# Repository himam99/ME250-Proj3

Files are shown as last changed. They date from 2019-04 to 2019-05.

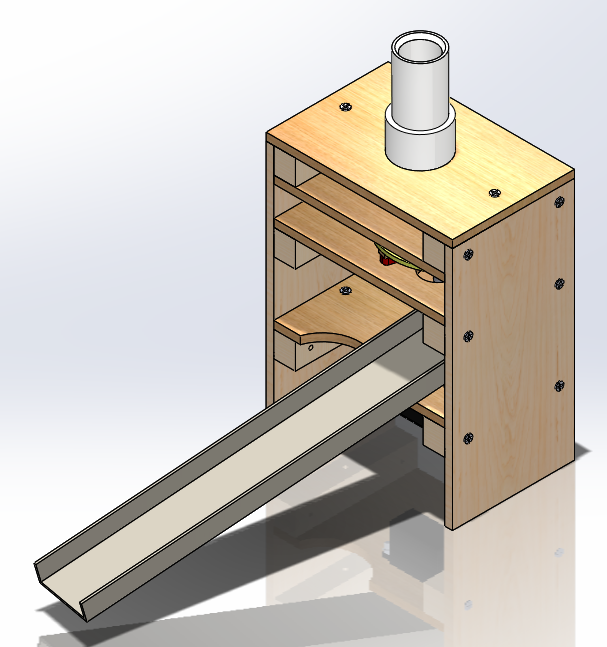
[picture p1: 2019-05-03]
LaTeX/Images/assembly_AB.png

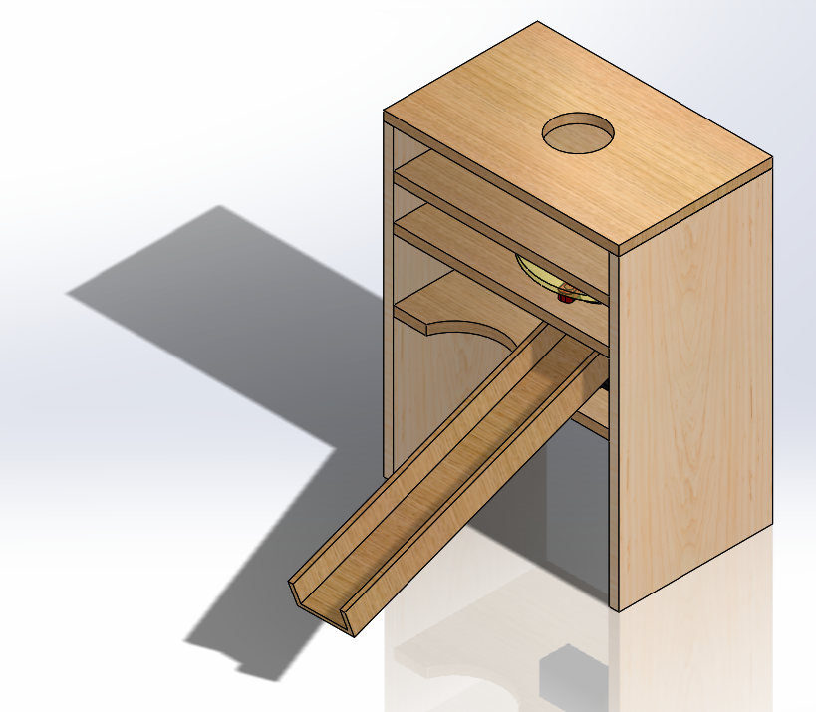
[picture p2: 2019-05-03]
LaTeX/Images/assembly_IP.png

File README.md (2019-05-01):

# ME250 S19 Project 3: Color Sorter

**Project 3: Color Sorter** for ME 250 at the University of Illinois at Chicago for the Spring 2019 semester.

This repository contains:
  - all Arduino (.ino) files used, either for testing or for the final product,
  - all CAD models (misc SolidWorks extensions), with different stages of development grouped seperately, and
  - all LaTeX files (.tex, .png for inset images, .pdf for output) used to generate the final report.
  
This project was made using Arduino, SolidWorks, Notepad++, and Overleaf.

Although this repository was created by me, some of its contents were made by other members of Group 17, and many other parts of the project could not have been done without their help.

Hammad Imam // himam4@uic.edu    
Group 17     
Undergraduate, Mechanical Engineering    
May 3rd, 2019

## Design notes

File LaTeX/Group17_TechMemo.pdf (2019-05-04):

# Project 3 Tech Memo: Color Sensor

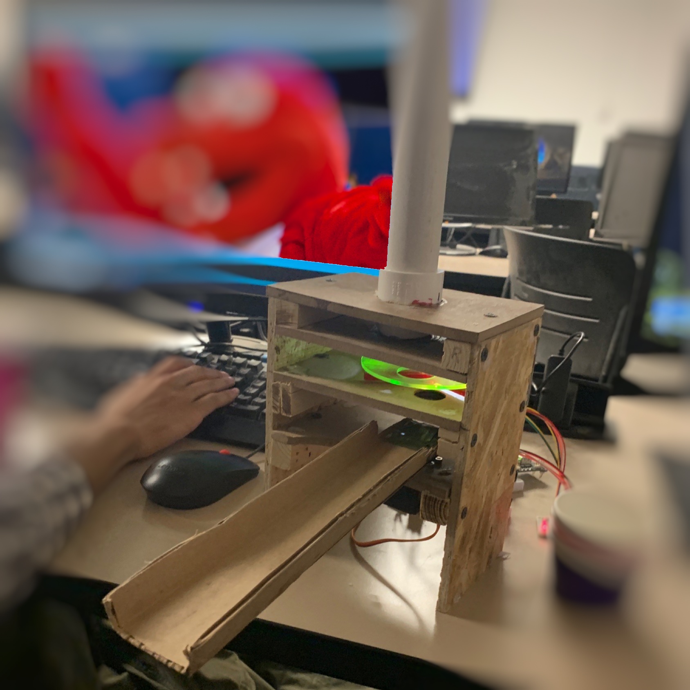
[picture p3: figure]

May 3rd, 2019.

# Team #17 The Three-Droppers Jos´e Luis G´omez Hammad Imam Thihan Moe Kyaw Daniel Spathies

# ME 250 Section #2 Professor Szwalek

## Executive Summary

The overall purpose of this project was to create a device that would sort balls by their color. This project is part of the curriculum for ME 250: Intro to Engineering Design and Graphics during the Spring 2019 semester at the University of Illinois at Chicago.

This report begins with an introduction on the background of the project. Next is the problem definition section, which details how the group identified constraints and objectives, and what metrics were used to define them. An objectives tree is given to detail how the group identified different objectives used in the development of the project. The problem definition section is followed by the functional analysis, which includes definitions of functions as well as a functions-means tree for the functions and means that the group brainstormed. Then, the report highlights how concepts were generated and narrowed down into the final design. The final design section is broken into mechanical, electrical, and cost subsections. The mechanical design subsection details how the physical aspects of the device were designed, from the initial sketch to a detailed CAD assembly. Dimensioned CAD drawings are provided to show more detail on the final product. The electrical design subsection describes how the components were wired and configured, and provides a wiring diagram so it can be seen how the wiring was done. It also contains a section on code which describes the main functions and algorithms used in the device. The final subsection of the final design is the cost, which provides both the dollar value of the constructed materials, and the environmental impact of the creation of the device. After the device design has been thoroughly explained, the changes and improvements made while testing are given so the stages of the design process can become clear to the reader. The report summarizes with a conclusion of the work done in the project and the lessons the group learned from working on it.

From the report, we can gather how a device like this might be created, going from how it was determined what it should do to how it was initially created to how it was modified to improve its performance. The major conclusions that can be drawn are that a project like this is very time consuming and requires good foresight so that nothing is unplanned for. Projects like this also require proper time management so that any issues that arise can be discovered and dealt with and still be completed in a timely manner. The major lessons learned from this project are both technical skills, as this project required coding, building, and testing knowledge that not all group members previously had; and time management skills, as many aspects of this projects went over the time constraints we had initially planned for. In the future, the group members will use these skills to improve their performance in engineering projects, both those related to academia and in industry.

Overall this project was a good learning opportunity for the team and a lot was accomplished. The device unfortunately did not have all aspects properly functional by the end of the project, but the group learned a lot through the design process and noticing what went wrong. This report aims to detail how the group went through the design process, what was changed during the design phase, and the lessons that were learned throughout the project.

## Contents

1 Introduction | 4
2 Problem Definition | 5
3 Functional Analysis | 7
4 Concept Generation | 9
5 Final Design | 17
6 Device Testing | 28
7 Conclusions | 29
A References | 30
B Code | 30
C CAD | 33

## 1 Introduction

This tech memo is on the creation of a color sorting device that should be able to sort rubber balls by their color. This project was assigned to the team through a mechanical engineering course, the limitations in concepts, materials, and functions of the device are created by the course project guideline. Material limitations are limited to what has been listed as acceptable in one of the handouts given by the course managers and instructors. The time for the brainstorming and development of the device was also limited as it was limited to when we were told about the nature of the project. This project is the summation and an application of much of the knowledge and skills that were taught in the course. There were two projects that involved writing a technical memo on a reversed engineered device and on an experiment. They served as practice for learning how to write a technical memo. The course had CAD Solidworks, Arduino UNO, and workshop lessons which would all be applied in this project. The manufacturing of the components of the device was limited to 3D printing, the courses’ workshop materials and tools, and laser cutting.

The main objective of this report is to give an extensive and comprehensive explanation of the process that was taken to create the final device given the limitations and primary objective. The sub-objectives of this report, which function to accomplish the main objective, can be divided based on each section of the report. The first following section is Problem Definition, the purpose of this section is to define what the problem is in a better sense by explicitly stating the limitations of the project, creating objectives of multiple levels, and metricizing those objectives to quantify the satisfaction of those objectives. The primary culmination of this section is the objectives tree which shows all of the objectives in their order of relation and importance. The following section is Functional Analysis which is where the team begins to define what the device will perform and the possible means by which the device can perform those functions, this culminates in a Functions-means tree which gives you a layout of how the functions and means are interconnected. The next section is Concept Generation and Selection, this section is where the expansion and then contraction of ideas is done to find the best possible design concept. The expansion is done by creating a morphological chart that lists all the possible means for each of functions of the device. The morph chart is then reduced by accounting for illogical and unreliable means combinations. From the remaining possibilities a list is created of the top twenty, then one of the top five with designs images for each of them. Finally, a comparison chart of the top five concepts is created to find the top device concept. The following section is Final Design. In this section the physical design process of the top concept is explained through CAD models and explanation on modifications. The software and hardware configurations are explained in detail and finally a Bill of Materials table is created which has physical, economical, and environmental properties of each of the parts of the device, excluding hardware and software. The next section is Device Testing, this section is where the findings of trials and the decisions of modifications to the device in light of these findings are documented. The section that follows is the Conclusion of the report which should review the findings of the report, state any of the limitations of this project and suggest any improvements that could be done to this project. Finally, the report ends with References and an Appendix containing detailed information on the software used.

## 2 Problem Definition

### 2.1 Introduction

This section of the report is meant to define and clarify the main problem of the designing of the device. The objectives, metrics, and constraints of the designing project are stated here as they give the main context needed to define the problem. The objective tree shows all the objectives of the device in hierarchical order and grouped according to their sub-sectionality of each other. All the ideas that have been generated by the designing team have been added to the objectives tree as the purpose of the objective tree is to give a graph of all the possible objective paths that can be taken to fulfill the primary objective.1 Affinity mapping was the method used to create the objective tree. This process begins by having the objectives generated through brainstorming possible objectives and writing each one down on a sticky note. These objectives are then sorted into categories and placed according to priority.

The team was tasked with creating a device to autonomously sort bouncy balls by color into a predetermined number of cups. Certain considerations must be taken into account in designing such a device like using the most eco-friendly materials, manufacturing at the cheapest price and making a safe usable device that functions without input from team members.

### 2.2 Definitions

Metric: A standard of measurement; in the context of engineering design, a scale on which the achievement of a designer’s objectives can be measured and assessed.

Constraint: A limit or restriction on the design’s behaviors or attributes

Objective: A feature or behavior that the design should have or exhibit

### 2.3 Metrics

Metrics are the quantification of the stated objectives, this facilitates a comprehension of the level of success of the objectives.

- Cost efficiency: cost in dollars
- Time Efficiency: Time in seconds
- User Experience: On a scale from one to ten, ten being the greatest ease of use, reusability, and transportation of the device
- Functionality: Based on the percentage of balls that were successfully sorted to the amount of balls to be sorted, how accurate or effective is this device at achieving its function
- Designer experience: Scale from one to ten, ten being the best and easiest device to construct and build.

### 2.4 Constraints

The constraints are the limitations to the means by which the device will function.The constraints for the building of this device are:

- The device must be attached to the storage bin(hopper).
- The materials that can be used are limited to the ones found in a list.
- The quantity of each of the materials is limited to what is set on the aforementioned list.
- Energy used to power the device is limited to mechanical, electrical, and/or chemical energy.
- The device must be able to perform its primary objective autonomously

### 2.5 Objectives Tree

The following diagram is the visual description of the hierarchical order, based on contribution to solving the problem, and sub-sectionality relations of all objectives of primary, secondary, tertiary, etc., order. between all the objectives.

Table 4.3.1 - Morphological Chart

The primary objective of the device is on the top of the diagram. It is to make a machine that can sort by color. The lowered ordered objectives are objectives that can facilitate this primary objective and/or are objectives desired by the designers. These objectives have been limited to those which can be metricized for evaluation of the success of each objective for further development. The four main secondary objectives are efficiency, user experience, designer experience, and functionality. Under these objectives there are multiple objectives that are subsections of these four secondary objectives. It should be noticed that none of the objectives in the objectives tree are necessary elements of the device. This is due to the clear distinction between objectives and constraints, as they are defined above. There is only one primary objective which is the main answer to the problem statement.

### 2.6 Conclusion

To conclude this section, the metrics, constraints and objective tree are the parts of this section which give the context of the problem, something important for final analysis on determining how to go about solving the problem. The objective tree is important for understanding the hierarchical order and subsectional relationships of the objectives. The metrics and constraints sections of this section are also important as they help the designer understand what they are limited to and how it is that they can evaluate the success of their objectives.

## 3 Functional Analysis

### 3.1 Introduction

This section is on the functions and means of the device. The primary functions that the device is supposed to perform as well as the sub functions that the corresponding means will need are listed. The meaning of functions and means as they are used in this report refer specifically to engineering design and so are defined in this section for clarification. The functions and means are presented in a tree diagram which is meant to highlight the ranking of importance/order of the functions and link the means to their corresponding function.

### 3.2 Definitions

(Basic/Primary) Functions- what a device is supposed to do, should be described using verbs.

Means- The ways by which primary functions can be implemented, should be described usingnouns.

Secondary/sub functions- Functions that are governed by the means of the basic functions[2].

### 3.3 Function-Means Tree

The function-means tree is meant to give order to all the types of functions and their corresponding means. The order is based on the purpose of the function. Functions that serve the purpose of mitigating or completing other functions are secondary functions. All others are basic primary functions. Figure 3.3.1 is the functions mean tree for this projects device. The tree starts by giving primary functions in bolded text in rectangular boxes. More specific functions that explain the pieces of the primary functions are then given in underlined text in rectangular boxes. Means for each function are in plain text trapezoidal boxes below each function. Additional sub functions specific to each means are then given in plain text in rectangular boxes.

Tree outline

- Power Device
- Contain Structure

– Resist forces

– Join main structure

- Load balls in from hopper

– Couple from hopper
– Release balls from hopper
- Sort by color

– Determine color
– Release from color determiner
- Send ball to cup

– Determine where balls go
– Aim ball to cup

– Move ball to guide
– Guide ball to cup
– Resist forces while guiding ball

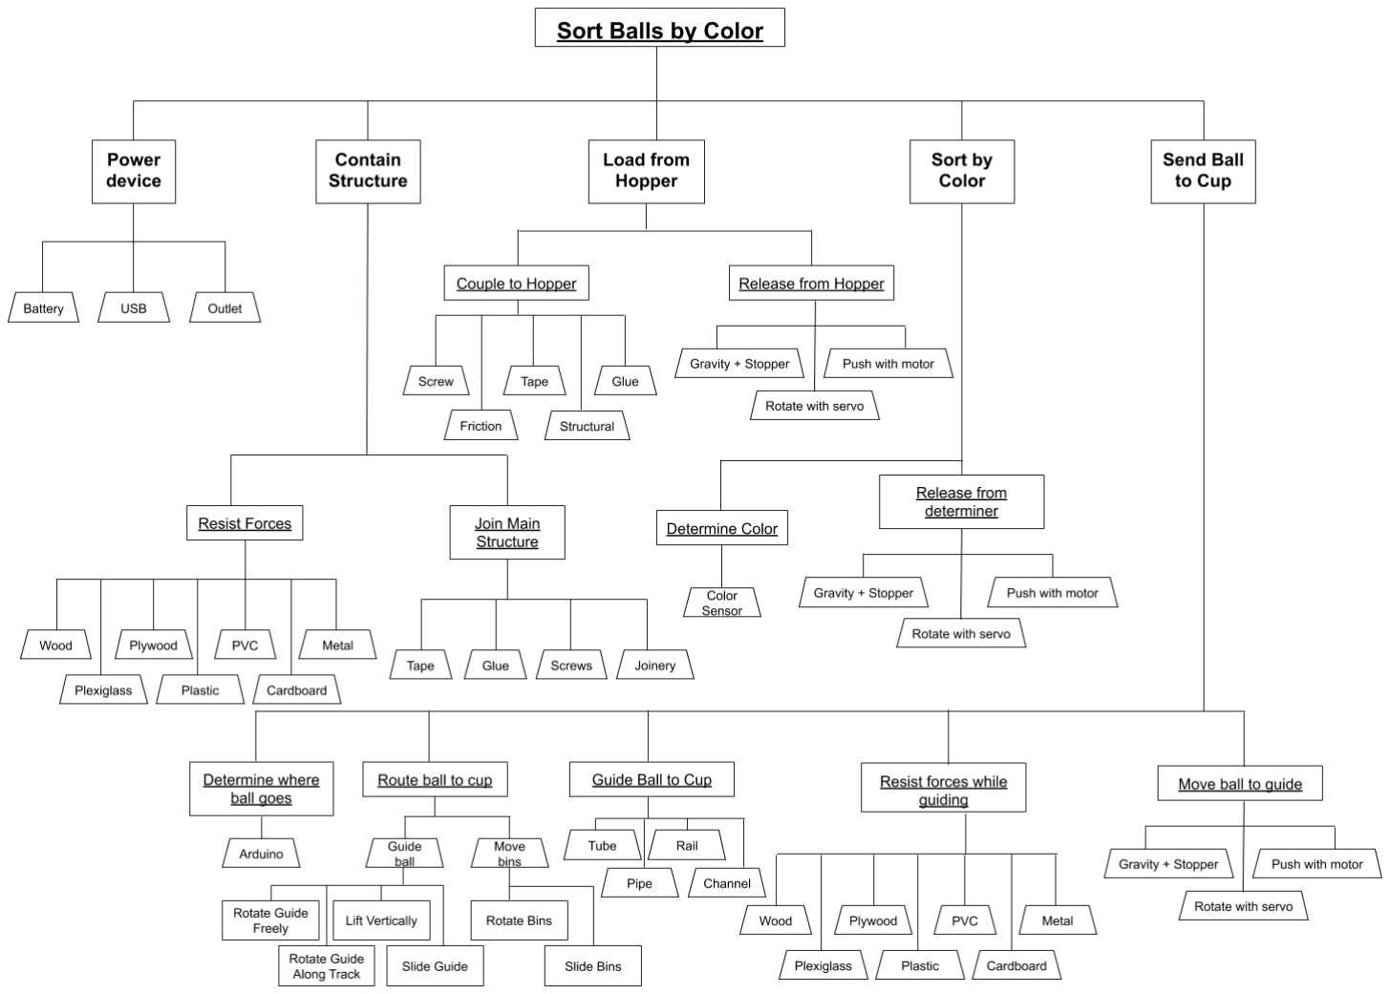
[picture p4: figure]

Figure 3.3.1 - Functions-Means Tree Full size available here. (https://raw.githubusercontent.com/himam99/ME250-Proj3/master/LaTeX/Images/functionmeans.png)

## 4 Concept Generation

### 4.1 Introduction

This section’s purpose is to present the procedure that was taken to select the concept design for the color sorting device. In this section, a morphological chart is used to generate all the possible design concepts by listing all the functions and their corresponding means. From this the top twenty or so concepts are chosen through an analysis on their practicality and ability to satisfy objectives. These concepts are listed in this section. From this a list of the top five concepts are chosen through more rigorous application of the same analysis as beforehand, these top five are also listed and justified. Finally, through the use of comparison charts the top concept is selected for manufacturing the device.

### 4.2 Definitions

Morphological chart: A matrix in which the leftmost column is a list of all of the principal functions that our design must perform and also some of the key features it must have.
Design space: An imaginary intellectual region of design alternatives that contains all of the possible solutions to the design problems[3].

### 4.3 Morphological Chart

The leftmost column of the chart shows the functions that should be included in the design. To the right of the functions are the all different types of means that were found which could perform the functions. The purpose of this chart, Figure 4.3.1 is to aid in expanding the design space.

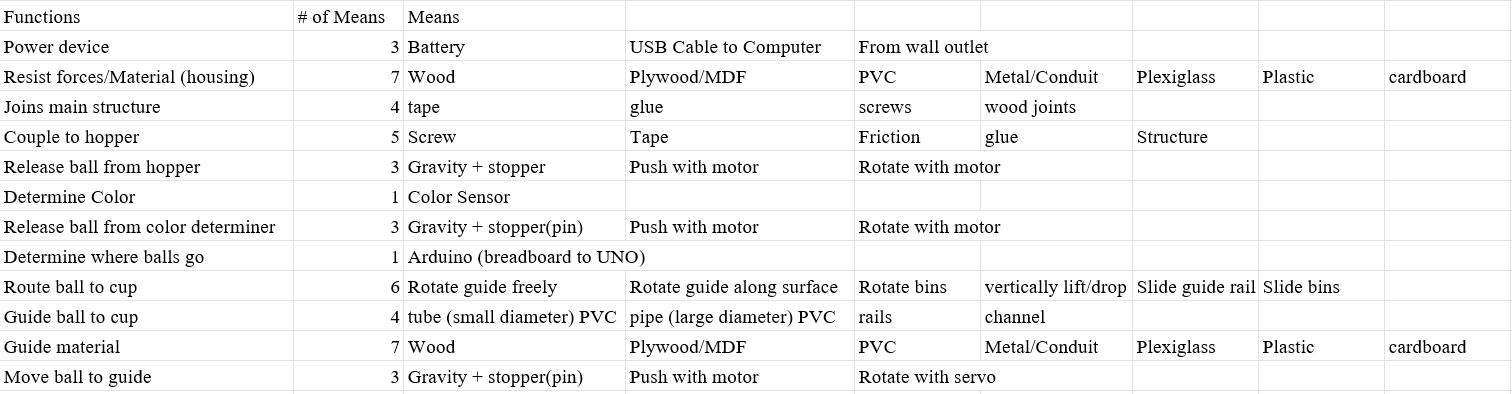
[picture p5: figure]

Table 4.3.1 - Morphological Chart

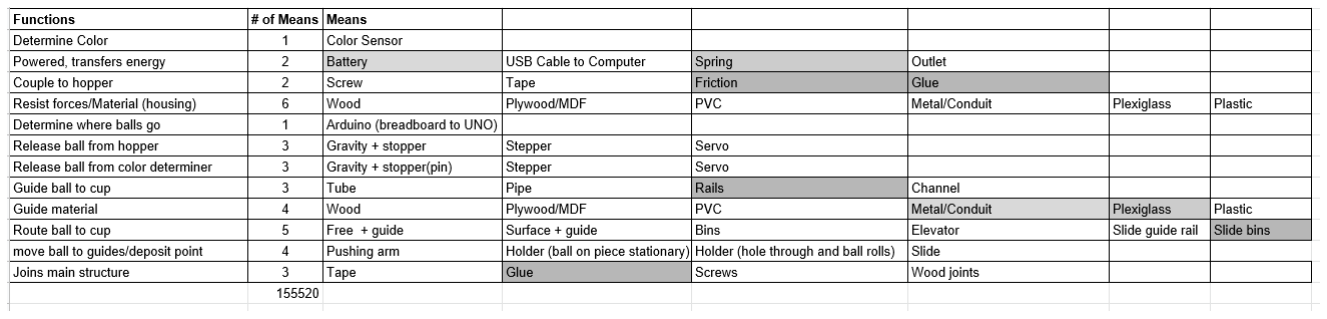
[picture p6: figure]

Table 4.3.2 - Reduced Morphological Chart

For Figure 4.3.2, the majority of the reductions in means are ones that are unreliable and impractical both relative to other means and somewhat objectively. For example, glue is not strong enough to withstand the forces on the main structure, so it was eliminated from the morph chart.

### 4.4 Concept List

- Wood housing using screws as main joiner, the color sorter is under the hopper, the ball then drops on an arm attached to a servo. The servo then rotates the calculated amount to one of the three fixed pvc pipes that lead to a cup.
- Cardboard housing using duct tape as main joiner, after color is sensed, a cardboard channel is moved by a servo to align with the proper cup and then the ball is released from the color determining area and then goes down the channel into the correct cup
- Wood housing with screws as main joiner, also there are fixed ramps made of cardboard, the ball moves from hopper to color sensor, then the ball gets released and gets deviated dependant on arduino code to go down a different ramp which will lead to a corresponding cup
- PVC housing with glue and tape as main joiners, this device acts as an elevator or dumbwaiter, after determining the color at the top of the shaft, this device drops the ball a determined height into the right cup, a servo with string can be used to lower or raise elevator shaft to desired position.
- Wooden housing with plastic, a spring and glue or tape as joiners, this device brings a ball from the hopper to the color sensor then drops it into a waiting catapult arm with a spring attached. The arm is pulled back at the precise distance to allow the ball to fly as a projectile and land in the correct cup, the arm is then winched back with a motor to an arduino determined distance and repeated.
- Wooden housing, a type of manufactured belt, metal to make conveyor and cardboard with various joiners being required. First, a single ball is deposited from the hopper and dropped onto a rotating conveyor belt that moves the ball to the right, the ball passes under the color sensor and the color is determined and then the arduino and code process the color and move a moveable ramp/platform at the end of the conveyor to bounce the ball into the correct cup.
- Wooden housing, a type of manufactured belt, metal to make conveyor and cardboard with various joiners being required. Similar to the other device using a conveyor, this device releases a ball onto the moving conveyor belt, scans the color and continues down the conveyor but next one of three motors is turned on and when it senses motion, extends to push to ball off the side of the conveyor into the correct cup.
- Wooden housing with screws or tape as main joiner, after scanning the color of the ball in the color scanning portion of the device, the ball is then dropped onto a ramp with a very small slope or angle and as the ball slowly travels down the ramp, the servo corresponding to the correct cup then moves and opens a hole for the ball to fall through into the cup below it
- Wooden housing with screws as main joiner, after ball’s color is sensed, the ball drops onto an arm attached to a servo, the arm rotates to be over the correct cup and then the servo on the arm activates, opening a hole in the arm, releasing the ball into the correct cup
- Cardboard housing with glue and tape and main joiners, the ball gets released from hopper, color gets sensed and then after being released from the color sensing station, the ball is redirected by a servo with an extended arm to push the ball down of of the three separate paths of the connected ramp into the desired cup

Top 5 Concepts

- Tri-Tube - Wood housing using screws as main joiner, the color sorter is under the hopper, the ball then drops on an arm attached to a servo. The servo then rotates the calculated amount to one of the three fixed pvc pipes that lead to a cup.
- Moving channel - Cardboard housing using duct tape as main joiner, after color is sensed, a cardboard channel is moved by a servo to align with the proper cup and then the ball is released from the color determining area and then goes down the channel into the correct cup

- Conveyor belt - Wooden housing, a type of manufactured belt, metal to make conveyor and cardboard with various joiners being required. First, a single ball is deposited from the hopper and dropped onto a rotating conveyor belt that moves the ball to the right, the ball passes under the color sensor and the color is determined and then the arduino and code process the color and one of three motors pushes the ball when motion is sensed into the correct cup
- Arm controller - Wooden housing with screws as main joiner, after ball’s color is sensed, the ball drops onto an arm attached to a servo, the arm rotates to be over the correct cup and then the servo on the arm activates, opening a hole in the arm, releasing the ball into the correct cup
- Tri-fold ramp- Cardboard housing with glue and tape and main joiners, the ball gets released from hopper, color gets sensed and then after being released from the color sensing station, the ball is redirected by a servo with an extended arm to push the ball down of of the three separate paths of the connected ramp into the desired cup

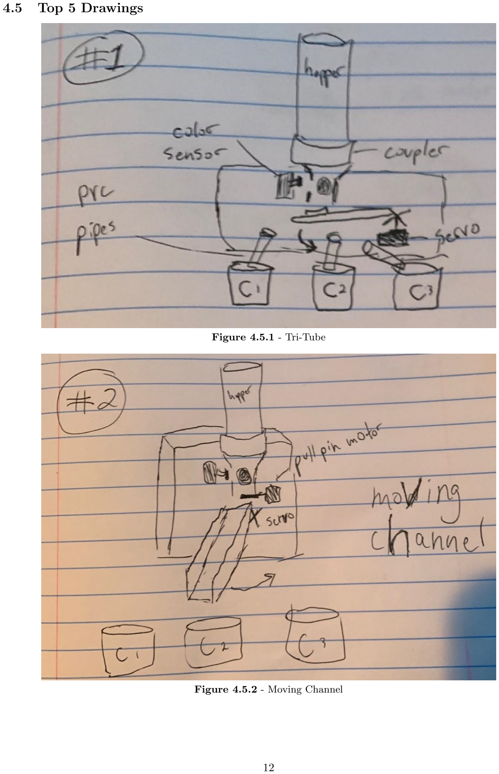
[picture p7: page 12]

### 4.5 Top 5 Drawings

Figure 4.5.1 - Tri-Tube

Figure 4.5.2 - Moving Channel

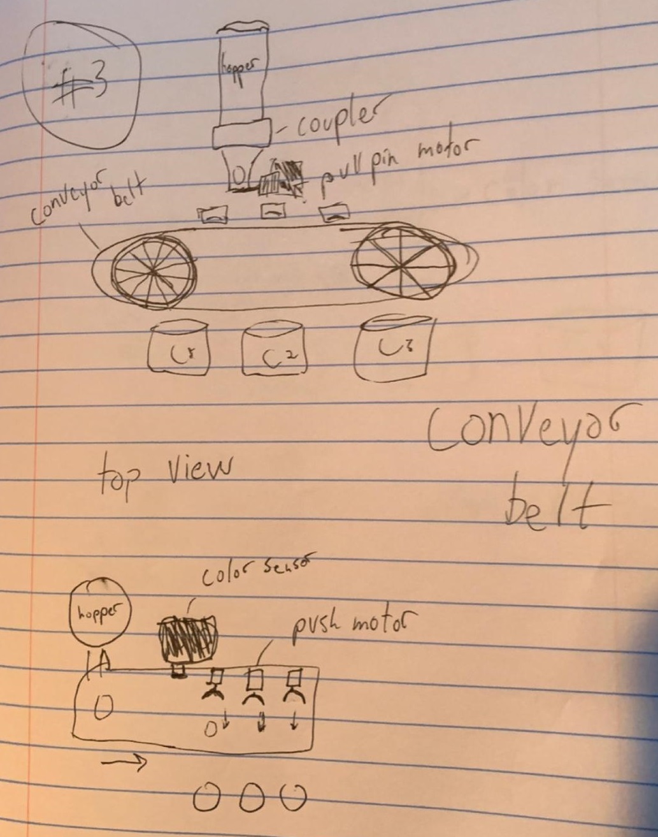
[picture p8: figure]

Figure 4.5.3 - Conveyor Belt

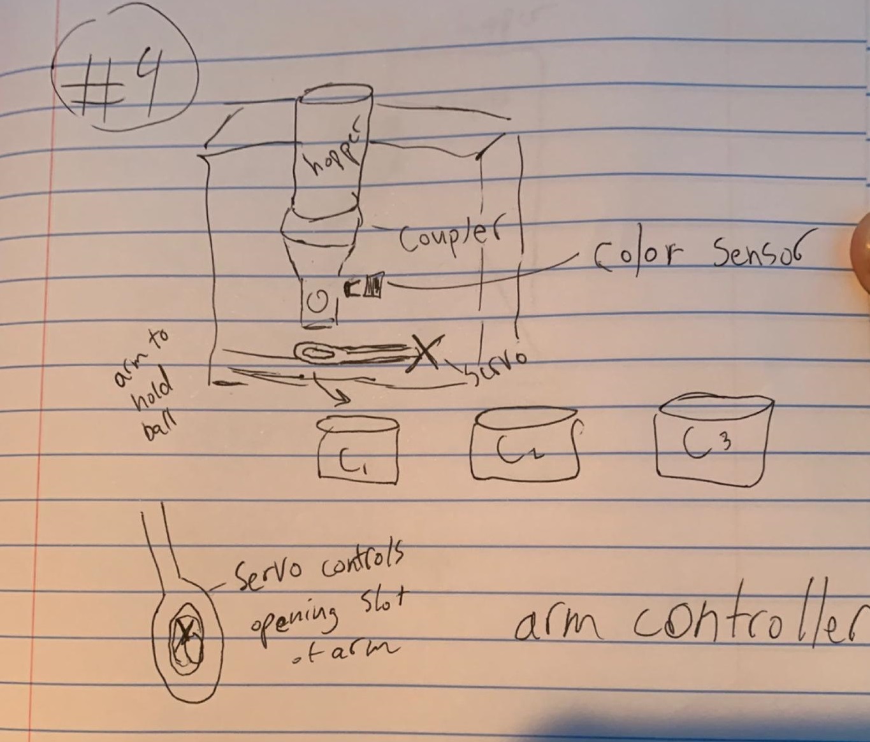
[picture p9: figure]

Figure 4.5.4 - Arm Controller

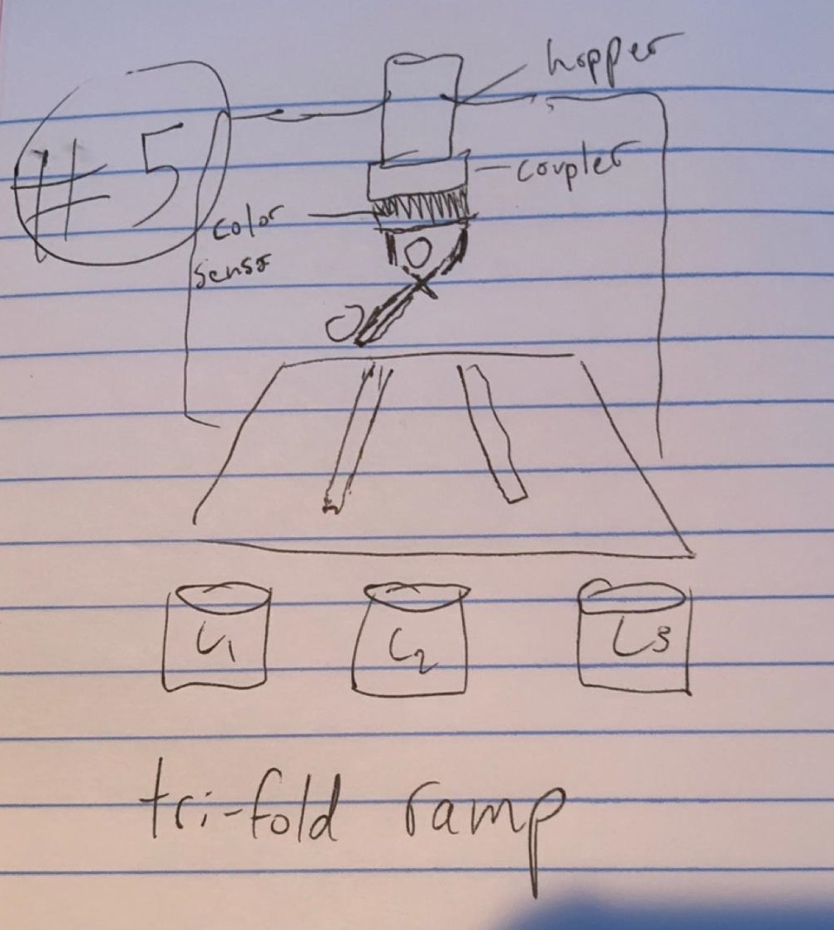
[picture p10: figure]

Figure 4.5.5 - Tri-fold Ramp

### 4.6 Comparison Chart

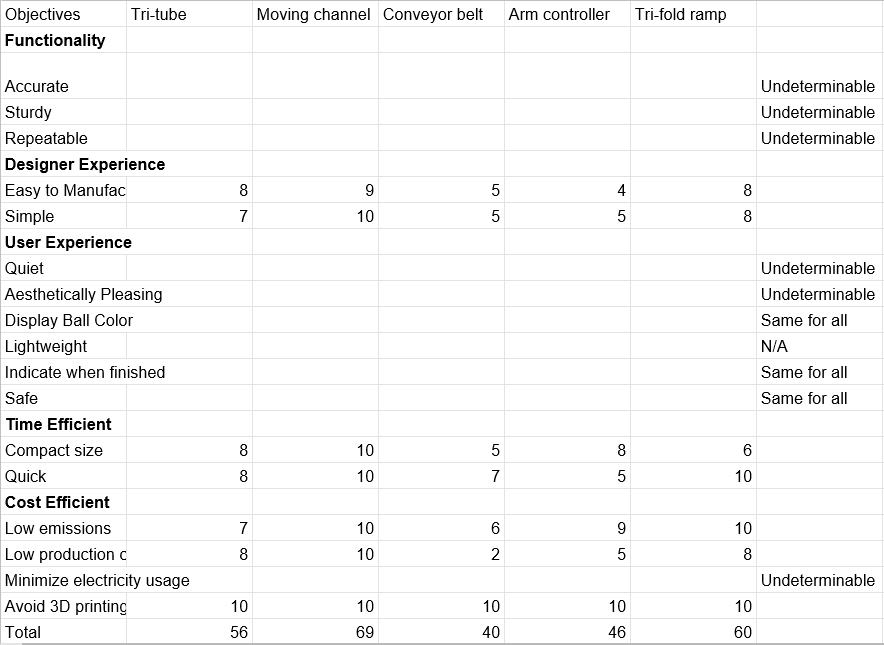
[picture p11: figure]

Table 4.6.1 - Comparison Chart

The above chart, Table 4.6.1, was used to compare the top five concepts to select the top three designs and the best design. Each objective that could be determined from the initial designs was ranked from 1-10 with 10 being the highest. The scores were then summed, with the top design being the one one the highest sum. Many of the objectives were given a rating of ”Undeterminable” if it was not possible to determine from the initial design. Notably, there was some difficulty in finding the appropriate way to predict many of the secondary objectives in the functionality objective. Other objectives were given a rating of ”Same for All” or ”N/A” if it was determined that all designs would perform roughly the same for that objective.

### 4.7 Conclusions

In accordance with the purpose of this section, the most important parts of this section are the morphological chart, the comparison chart and the concepts lists and explanations for reductions in means. The morphological chart is of great importance as it is what is primarily used in order to generate all the different types of concepts. The explanations of the process taken to reduce the number of possible concepts is of great importance as it is how we come to closer to a limited amount of concepts. The comparison chart is of great importance as well as it presents the rankings that we performed in evaluating the best concept. Using the comparison chart we ultimately arrived as the moving channel concept as being the best as it ranked best in cost and time efficiency and was also the top performer in the objective of designer experience. This design was chosen to be our final design and will be detailed more thoroughly in the ‘Final Design’ section.

## 5 Final Design

### 5.1 Introduction

This section documents how the design was created from the original concept. The first subsection is the mechanical design, which details how we came up with the physical construction of the device, how we designed it with CAD, and how we created it; it includes CAD drawings of the design at different stages of development and explanations and rationale for why those changes were made. The second subsection is the electrical design, which contains detailed explanations of both how the hardware was configured and how the software was designed; to illustrate the electrical design, both a photograph and wiring diagram of the circuit are provided. Finally, the third subsection is the cost, which breaks down how expensive the device was to produce, based on both a bill of materials with dollar value and an environmental impact report that finds the footprint of each individual component.

### 5.2 Mechanical Design

### 5.2.1 Preliminary Design

The team wanted to minimize the materials used and use materials that were as cost effective as possible. Keeping in mind that the hopper would be able to be suspended above the device, the team decided to use a gravity fed device that would take one ball at a time, drop it into a rotating plate connected to a stepper, scan the color of the ball, drop it through a hole into the next sub level and then the ball would drop onto the ramp which is connected to a servo motor that rotates the ramp to be above the correct cup. This design incorporated MDF wood for the housing, screws and glue as the joiners and cardboard, wood and PVC for the internals. Using the Arduino and a color sensor, the device is able to sense and redirect a ball to the correct cup. The device was built hoping to achieve the objectives as efficiently as possible.

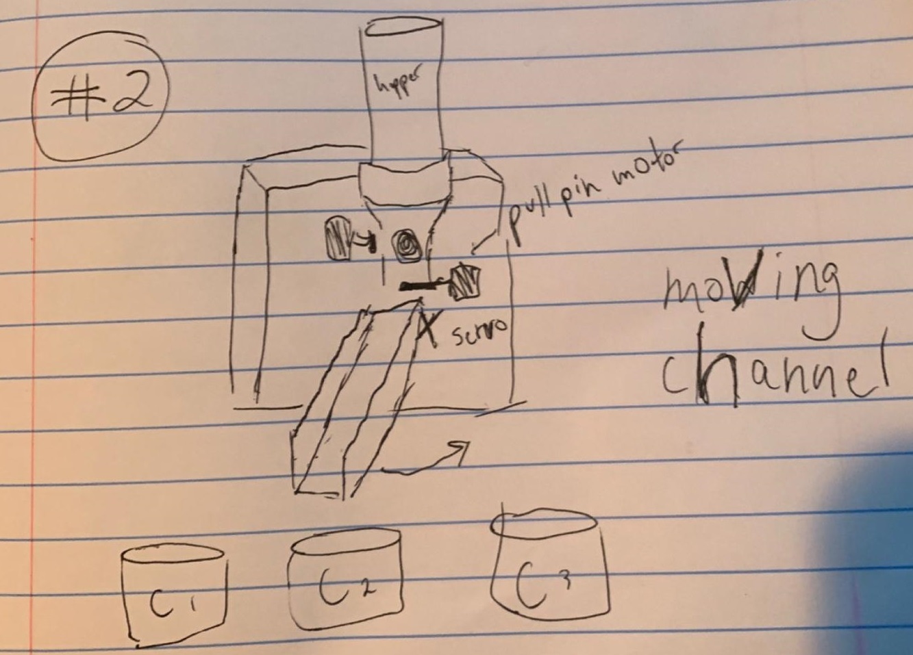
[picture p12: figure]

Figure 5.2.1.1 - Moving Channel

### 5.2.2 Prototype

This design was the first attempt at recreating the idea from the drawing in CAD. The device is made mainly using 1/8” plywood, except for the stepper horn which is 3D printed. The top plate of the device has a large hole which can hold the outside diameter of the hopper, followed by a plate with a small hole that does not let the hopper tube pass through but lets the balls through. Below that, a stepper motor rotates a plate with 3 holes. This middle plate is close enough to the hole that a ball cannot drop down from the upper plate unless the hole in the wheel is aligned with the hole in the upper plate. The wheel then rotates the ball along the middle plate until is next to the color sensor, which detects the color of the ball and sends it to the Arduino. Next, a servo motor attached to the ramp via a ramp bracket rotates so that the ramp points towards the correct bin. The wheel rotates again, which simultaneously loads in another ball, rotates the previously loaded ball to the scanner, and rotates the just-scanned ball to a hole in the middle plate where it will fall onto the ramp and roll into the correct bin. The lower plate has a hole cut to house the servo, as well as a small round cut in the side of it so that the ramp has a wider range of mobility before it hits the plate. The pieces were mostly to be glued together to avoid the need for lots of fasteners such as screws and bolts. Overall the prototype design was a first draft at realizing the initial drawing and helped us conceptualize how our design would work before we built it.

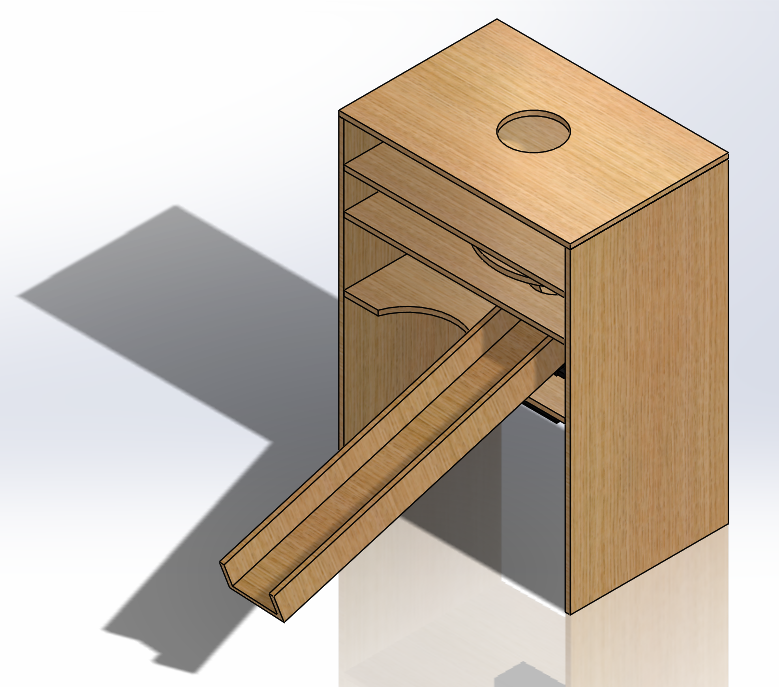
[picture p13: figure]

Figure 5.2.2.1 - Prototype CAD Assembly

5.2.3 “In Progress” Redesign

This design was created after the initial design when the group moved from the designing phase to the building phase. The most notable change was that all the wood pieces are now made of 1/4” wood instead of 1/8” like the original design, and the wheel is made of 1/8” laser-cut acrylic instead of hand-machined plywood. The wood was changed to 1/4” plywood both because the group determined 1/8” may not be sturdy enough, and because the lab did not have a large enough supply of 1/8”. The wheel was switched to laser-cut acrylic since the group determined it would be too time consuming to accurately cut a circular wheel by hand. Overall, the design remained mostly the same, with only some changes made to better reflect the work environment that the group had access to.


Figure 5.2.3.1 - “In Progress” CAD Assembly

5.2.4 “As Built” Design

The “As Built” design is notably different from the previous iterations. The most drastic change is that the pieces are now attached using screws instead of glue, which required some mild redesigning. The materials used were primarily OSB and MDF, which both would not hold well if a screw was drilled into the side. To fix this problem, supports were created out of 2x4s, which then had holes drilled into them to attach the pieces together at right angles. To space the section with the wheel properly, the upper plate was moved to be flat against the same support beams used for the top plate. Other small changes included the ramp material changing from plywood to cardboard since it was easier to create and weighed less, causing less strain on the servo. The color sensor was also relocated from the side wall to above the wheel so that it could get a more accurate reading as well as being more easily mounted and managed. The hole in the upper plate was widened to make room for a PVC coupler that could hold the hopper, as well as featuring a diversion ramp that ensured the ball was in the correct spot.


Figure 5.2.4.1 - “As Built” CAD Assembly

Screenshots of dimensioned CAD drawings are available below since this was the final iteration. For the CAD files of other development stages, or for the full sizes of these drawings, see Appendix C.

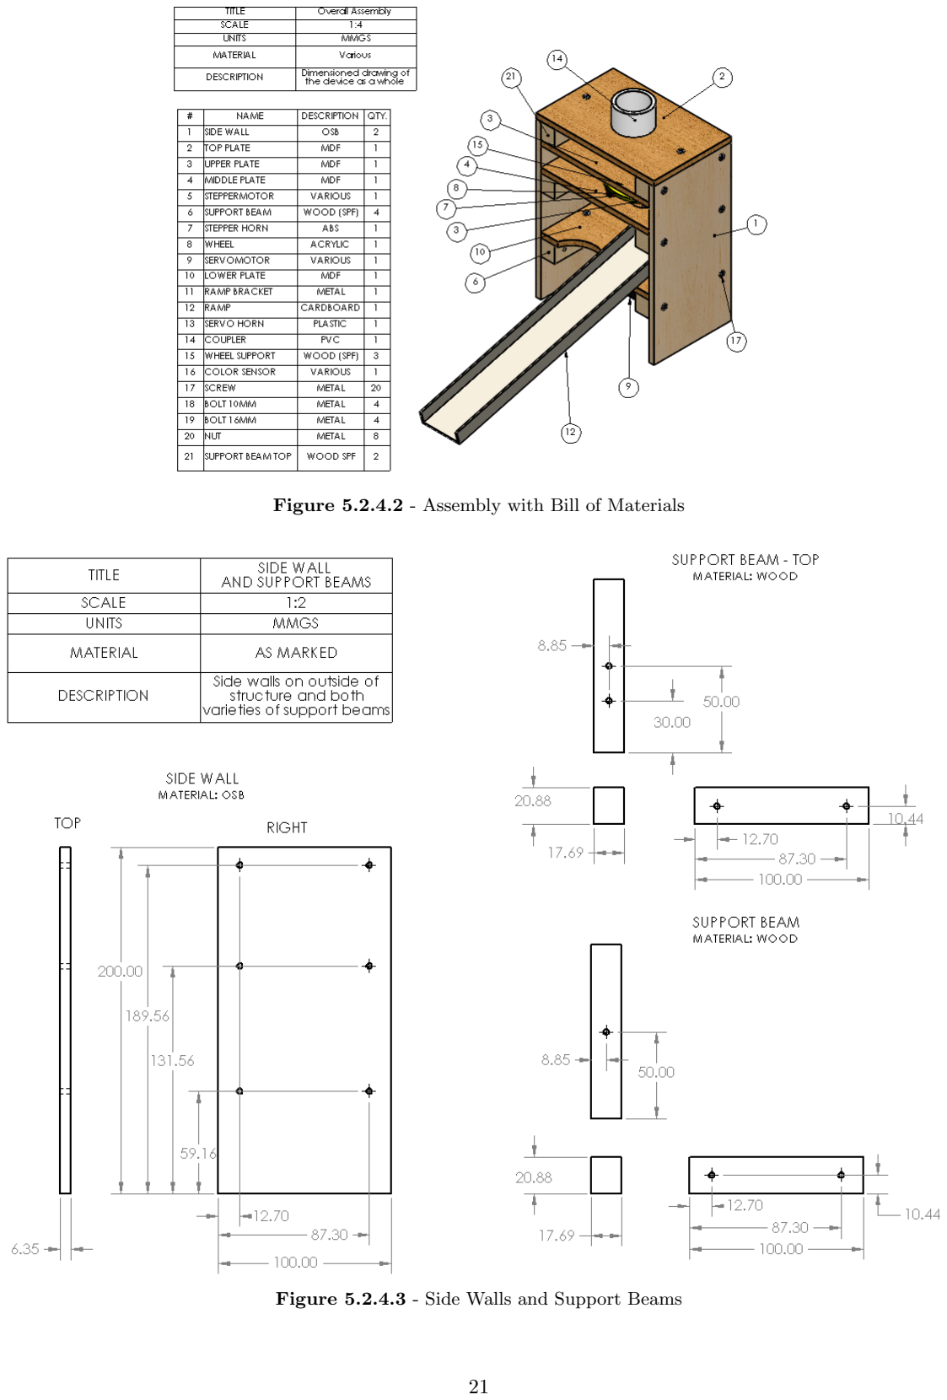
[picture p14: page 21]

Figure 5.2.4.2 - Assembly with Bill of Materials

Figure 5.2.4.3 - Side Walls and Support Beams

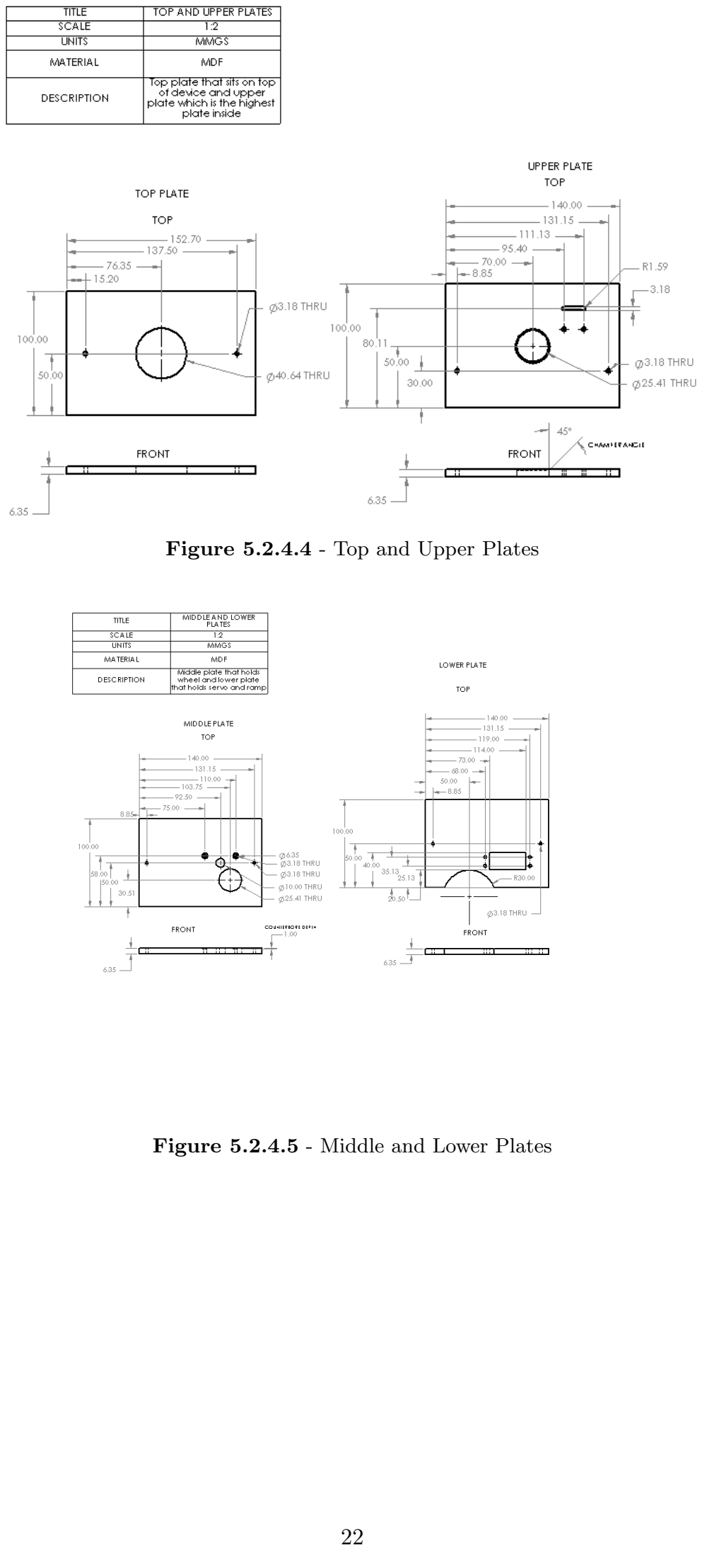
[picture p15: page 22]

Figure 5.2.4.4 - Top and Upper Plates

Figure 5.2.4.5 - Middle and Lower Plates

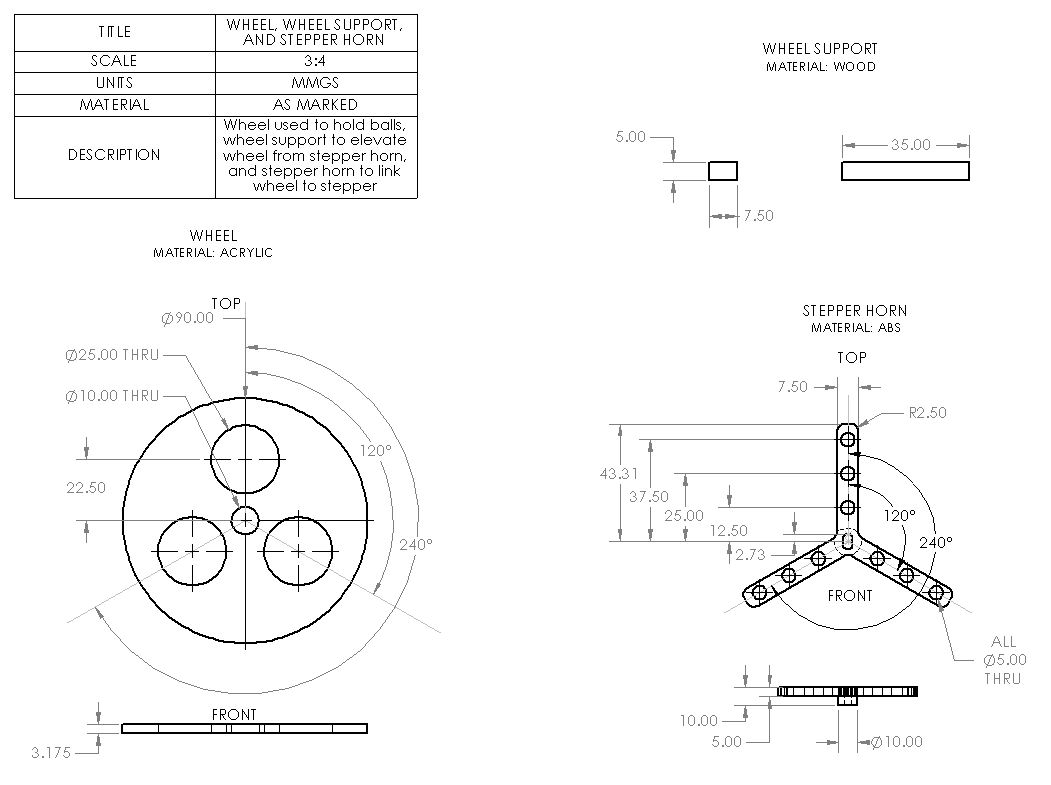
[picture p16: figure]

Figure 5.2.4.6 - Wheel, Wheel Support, and Stepper

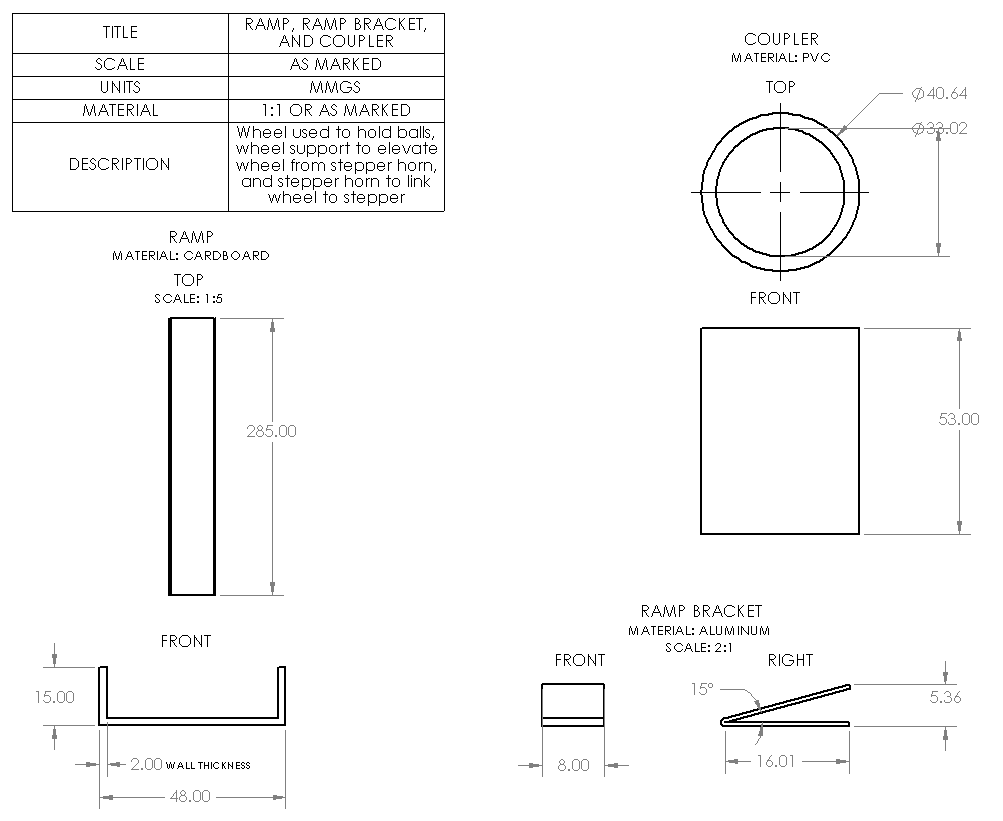
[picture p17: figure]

Figure 5.2.4.7 - Ramp, Ramp Bracket and Coupler

### 5.3 Electrical Design

### 5.3.1 Hardware

The following section will describe the hardware used for the project. The table 5.3.1.1 shows the quantity of hardware and the description of each piece, and figure 5.3.1.2 shows a circuit diagram of the hardware.

# | Name | Qty | Description

1 2 3 4 5 6 7 8 | Arduino Small breadboard RGB LED Stepper Motor Servo Motor Resistor Color Sensor Power Supply | 1 2 1 1 1 1 1 1 | Controls the device Connect hardware Shows signals from Arduino Rotates wheel Rotates ramp 10kΩ, protects LED from blowing out Reads color value Supplies power to motors

Table 5.3.1.1 - Circuit Materials

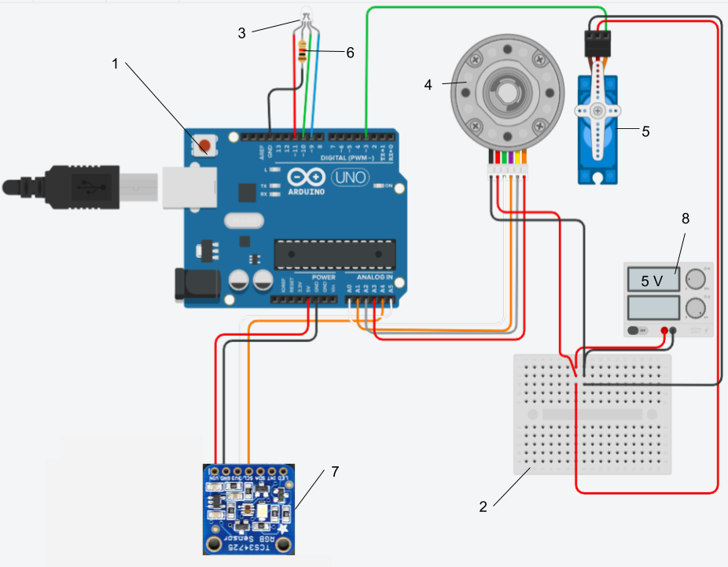
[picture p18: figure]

Figure 5.3.1.2 - Circuit Diagram

The hardware was designed to be as minimalist as possible given what was necessary. Our design called for one form of stepped continuous rotation and one form of motion that set an angle, so one stepper and one servo were used. The TCS sensor was used to sense the color of the ball. An RGBLED was also used for signalling so that the process could be displayed to the user. The TCS and RGBLED ran off the power provided by the Arduino, while a separate 5V DC power supply was required to run the motors. The circuit design originally did not include the power supply, but there were issues with power draw that neccessitated the addition of the power supply. Other than that, no other modifications were made to the circuit design since the start.

### 5.3.2 Software

The software for this project was written in two attempts. The first attempt was a prototype code and largely consisted of a long string of if-elseif-else statements that would check if the ball was within a certain color value and then set the servo to route the ball to the correct spot. While it’s possible this code could have functioned properly, it was hard to configure since the values that would need to be changed were in different places, and it used a confusing system of boolean variables. Additionally, this code could only be configured for option A and the group had decided to try option B. Ultimately this code was not used in the final testing.

The second version of the code was much more streamlined, and used custom functions. It began with a ”config” section that had all the pins that needed to be used and all variables that were used in the body of the code. Then, the setup() section was used to set up pins and initialize motors and the color sensor. The void() section was the main part of the code, with a for loop used to check the sensed color against stored variables to determine what color the ball was, and a nested for loop to check the bins for which places needed what balls and to route the balls there. Multiple functions were custom defined for the sake of saving space while writing the code. This also proved to be very useful since longer processes that needed to be repeatedly written, such as making the LED blink, were simplified into a single function that could be called with much less typing. More detail on the code is given below.

A unique aspect of the software used for this project was that a custom struct called ”ballColor” was defined. Each color ball had its own ballColor that contained the color name as a string, an array with expected RGB values from the color sensor, and an array with RGB values to display on the RGBLED. The structs were then compiled into an array called ”balls” so that balls[0] could call the first ball struct, balls[1] could call the second ball struct, and so on. This process was repeated for the bins with a struct called bin type so that the bins could be called in a similar fashion. The code uses this process so that the code could use a for loop to iterate through all balls instead of each ball needing to be typed out in the code.

To start, a function called checkColor() was written to simplify checking the color of the ball. The function would compare the color of the sensed component to a stored array for red, blue, and green values. If all 3 conditions were met, then the function would return true. This function was used as a quick way to check ball colors since checking these values one at a time would take a longer time. By writing this function, checking a ball color was able to be the condition for an if statement which made it much easier to check the ball color.

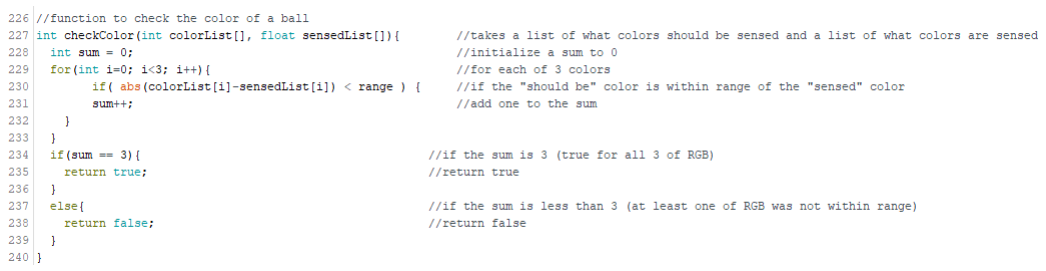
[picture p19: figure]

Figure 5.3.2.1 - checkColor() function

The code also used two functions for RGB output. The first was colorWrite(), which took an array of RGB values and displayed them on the RGBLED using 3 analogWrite() functions. The second function was colorBlink(), which took an array of RGB values and an integer. colorBlink() would pass the array to the colorWrite() function and turn the LED on and off for 250ms each for the number of times that it was given. These functions were used to signal with the RGBLED what was going on with the device. Integer arrays for red and white colors were also created to simplify the process since those colors were used for signalling often.

Figure 5.3.2.2 - colorWrite() and colorBlink() functions

The void loop() section began by rotating the wheel and taking input from the color sensor and storing it as a list called sense[]. To check the color of the ball, a for loop was written that would iterate through each ballColor struct and check the expected color values against the sensed values, blinking the LED once for every color checked. If any of the colors checked out, the variable ”color” would be updated to the color that was detected, the LED would blink the color of the ball, and the number of balls known to be in the hopper would decrease by one. If no balls were detected, the ”color” variable would be updated to ”none” and the LED would blink red once.

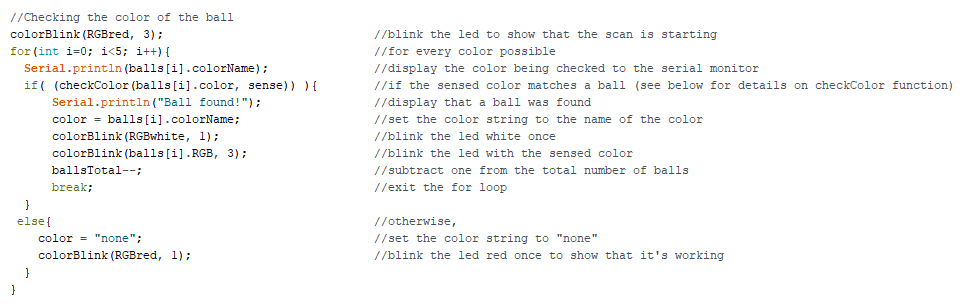
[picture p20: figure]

Figure 5.3.2.3 - Code to check the color of the ball

Routing the ball was a little bit more complex. A set of nested for loops were contained within an anonymous function. The for loops were iterated to check the sensed ball against every spot that could be open. If a match was found, the servo would be set to that bin, and the anonymous function would be exited. If no matches were found, the for loops were exited, which allowed a small snippet of code to run, setting the servo to the trash, before the anonymous function was exited. After this, both the number of balls sorted and balls left in the hopper would be checked to ensure accuracy. If both were 0, the code would stop.

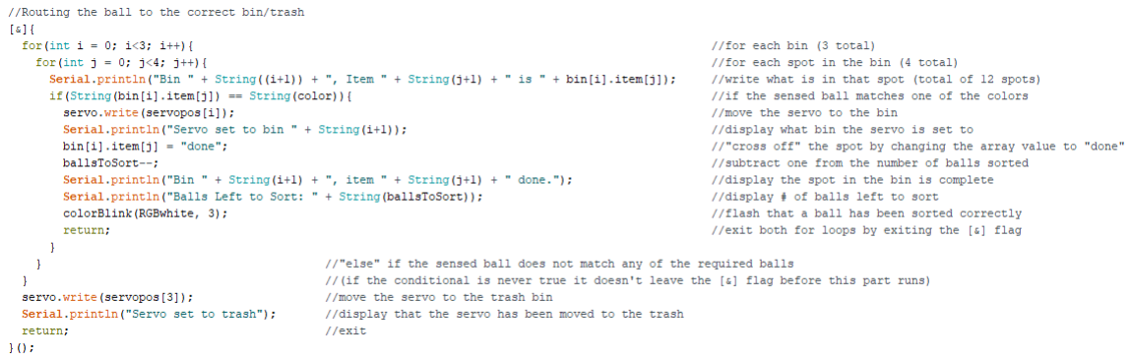
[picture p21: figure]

Figure 5.3.2.4 - Code to route the ball

The full code, as well as other Arduino files used for testing, can be seen in Appendix B.

### 5.4 Cost

### 5.4.1 Bill of Materials

Figure 5.4.1.1 below lists all of the parts that the device is composed of and how many of each part is used. Of each part the volume, vendor, cost, total energy and carbon footprints, embodied energy, carbon coefficient and mass is given. The volume is in mm cubed, the mass in kg, and the cost in 2019 USD. The total cost of the device is calculated to about $1.63. This does not account for the cost of the hardware and other pre-fabricated pieces, it only accounts for the cost of manufactured pieces such as the MDF and acrylic parts.

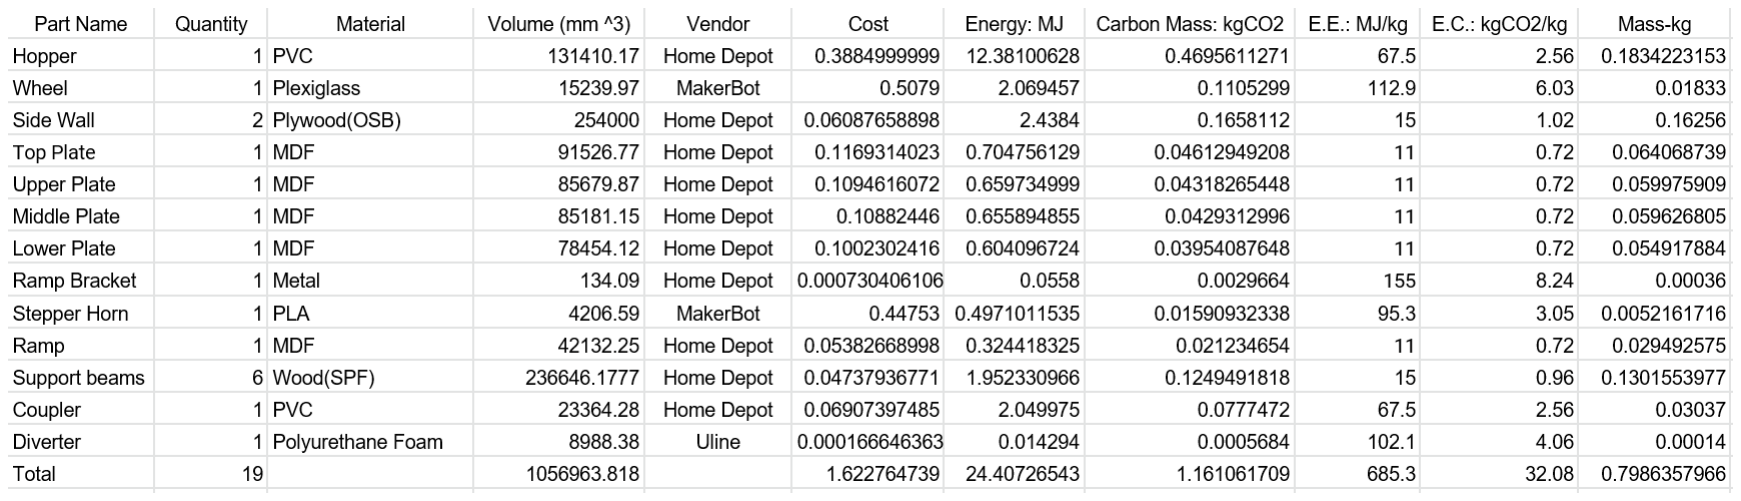
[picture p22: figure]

Figure 5.4.1.1 - Bill of Materials

### 5.4.2 Environmental Impact

The total embodied energy and carbon of the device are 24.407 Megajoules and 1.16 grams CO2, respectively. These values are relatively very low when compared to the global EE and EC of industrial and travel phenomenon. The embodied energy and carbon mass of every part can be found in the Bill of Materials. The part with the highest carbon mass footprint is the hopper, this is due to a relatively medium range carbon coefficient and large mass. The hopper is also the part with the greatest energy used to compose as it’s embodied energy is relatively moderate. Many other parts, specifically the metals and plastics had the potential to have a higher amount of carbon mass and energy as they had relatively high embodied energies and carbon coefficients but were stopped due to a relatively low use of the material.

## 6 Device Testing

This section of the report highlights the details of the testing period and the improvements made during the construction process as a result of tests.

The first prototype of code involved using many if-else conditions and had a large amount of boolean ex-pressions. The values for testing the balls were spread out, and the structure of the code was very repetitive. The second iteration of the code was made more streamlined by incorporating subfunctions and nested for loops to complete the same task more quickly. Additionally, all information for the balls was stored in custom-defined structs so that the process for checking the balls was more iterative and didn’t require code that was as long.

One of the issues the group noticed while testing the code was with the code for the stepper movement. Because the device uses a 3-location system, the stepper motor needed to rotate 120 degrees every rotation. However, the stepper motor uses a PWM signal out of 2048, which is not divisible by 3. Over time, the slight amount of offset from a full rotation would cause the wheel to become misaligned from the holes cut in the fixed plates. To solve this problem, the code uses a modulo 3 system to make sure that the balls are rotated twice by slightly over 120 degrees and once by slightly under 120 degrees so that every 3 rotations adds up to 360 degrees.

Another issue was with the power supply. Our initial plan was to run the motors off the power from the Arduino, but the current draw from the servo and stepper was too large and would cause issues with the color sensor shutting off and the motors not functioning properly. To solve this problem, a separate 5V board powered by a 9VDC power supply was used to run electricity to the motors, with power from the Arduino being reserved for the LED and the color sensor.

The biggest issue the group encountered was balls getting stuck in certain spots. The first point of issue was from loading in from the hopper. To solve this, a coupler was added with a small diverter made of foam that would funnel the balls to a specific spot instead of letting them roll around the pipe freely. This solution greatly reduced the amount of jamming when loading. The balls also got stuck when they were rotated by the wheel, which sometimes caused them to push the wheel off center and sometimes even pop it off. Different methods such as smoothing the surface area and changing the height of the wheel were tried, but the final design included adding small wooden pieces against the holes in the wheel. This design increased the contact area on the ball, as well as reducing the space it could slip into, which greatly reduced jamming on the rotation platform.

Unfortunately, due to time constraints, the group was unable to adequately test the project, so we were unable to produce any experimental data. There were many issues with the balls jamming which prevented us from completing a full test cycle. However, we were able to learn many lessons from this project which will help us with future projects.

## 7 Conclusions

To conclude the final design is able to function appropriately with the hardware and software to achieve the main objective and sub-objectives. It is able to do this through the functions that it was designed to do. The cost and energy and carbon footprints of the device are low as the device did not utilize a relatively great amount of material. Multiple issues with the running of the device did occur but they were solvable through creative modifications. Examples include, the addition of a coupler between the device and the hopper, the opening of the hole through which the ball goes to on its way to the rotary wheel, the power supply of the Arduino motors and the rotation angle of the rotary wheel. However, the basic concept of the final design was not altered. One of the main limitations on the determination of environmental impact of the device was that the embodied energy and carbon coefficient of many of the hardware and software parts was difficult to assess as they are composed of multiple materials. The final design was still in need of multiple changes from when it was first selected through the comparison chart. Most of these problems stem from actual application to the physical device issues, small imperfections in the manufacturing of the parts would lead to problems like the jamming of the rotary wheel or the rubber balls. The team found that dependence on a complex code is very perilous as finding the issue with the code could become more difficult then recreating it.

In the future, perhaps less emphasis could be placed on the complexity of the code. In general, it is better for the physical design of the device and the code to be as least complex as possible as application problems usually occur and the designs that are simpler are much more easily solved. A possible improvement in the project could be to utilize a software that could model the functions of the device so that the designers can see any possible issues with the design in application. Another suggestion is to give more leniency on the number of designs that could be created. If more designs were created the team could find the device that has less of a susceptibility to application problems. It is somewhat difficult to visualize this susceptibility in each of the top devices when the design concept is only an idea. Perhaps it would help if more attention was placed to the coding software for the color sensor and movement of motors earlier in the project so that more time can be placed on other aspects of the project such as the physical device design. If there were less limitation through the form of charging of costs on 3D printing, laser cutting, and the environmental impact of the device the primary objective could perhaps have been more achievable with all of the functions of the device being rated higher in terms of their success in achieving the objectives.

## Appendices

## A References

[1] C. L. Dym, P. Little, and E. Orwin, “Engineering Design: A Project Based Introduction 4th Edition,” pp. 92.
[2] C. L. DYM, P. Little, and E. J. Orw, “Engineering Design: A Project-based Introduction,” pp. 71–81, Oct. 2013.
[3] C. L. Dym, P. Little, and E. Orwin, “Engineering Design: A Project Based Introduction 4th Edition,” pp. 92.

## B Code

B.1 Screenshots of Code

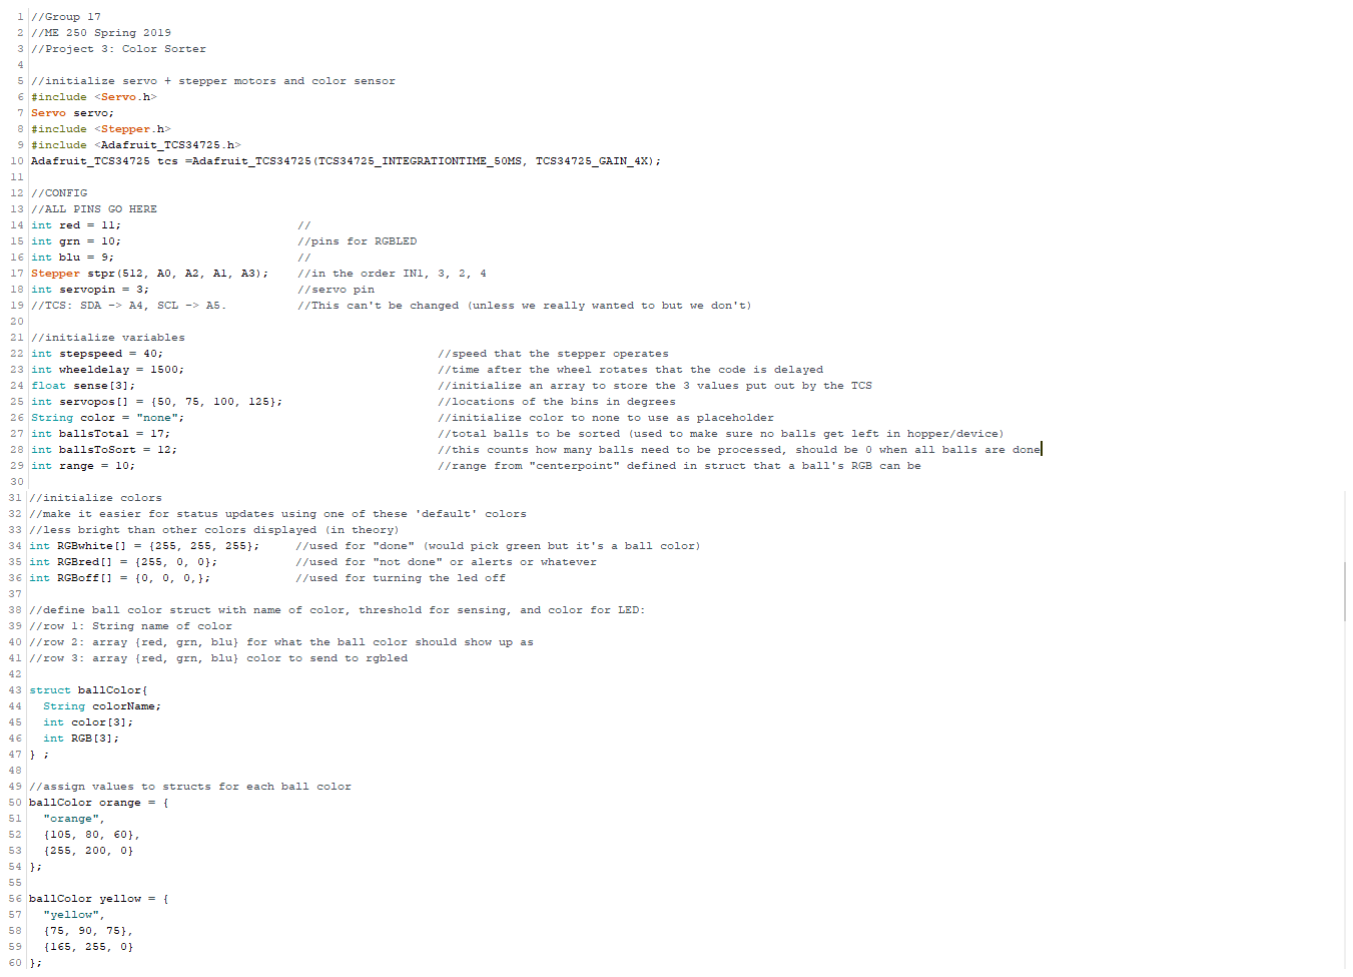
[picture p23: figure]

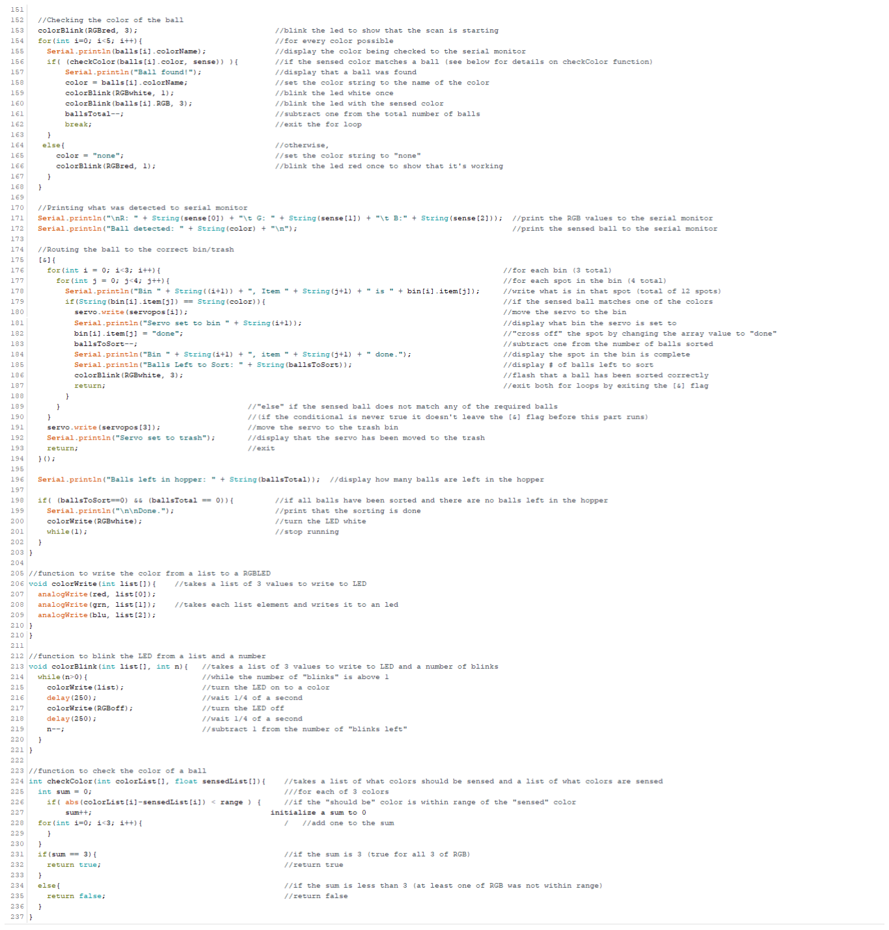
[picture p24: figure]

B.2 GitHub

Code for this project was maintained in a GitHub repository by Hammad Imam. The main Arduino code used in this project can be seen in more detail here. (https://github.com/himam99/ME250-Proj3/blob/master/Code/me250_proj3_code/me250_proj3_code.ino) Other code used in the development and testing of this project can be found here. (https://github.com/himam99/ME250-Proj3/tree/master/Code) Any questions about the GitHub repository can be sent to himam4@uic.edu.

## C CAD

C.1 Sources

All CAD work for this project was done in SolidWorks. CAD models for the stepper, servo, and TCS were found on GrabCAD.

C.2 Additional Files

All drawings for the “As Built” design are given above. The original part and assembly files, as well as the files for previous iterations of the design, can be seen here. (https://github.com/himam99/ME250-Proj3/tree/master/CAD)

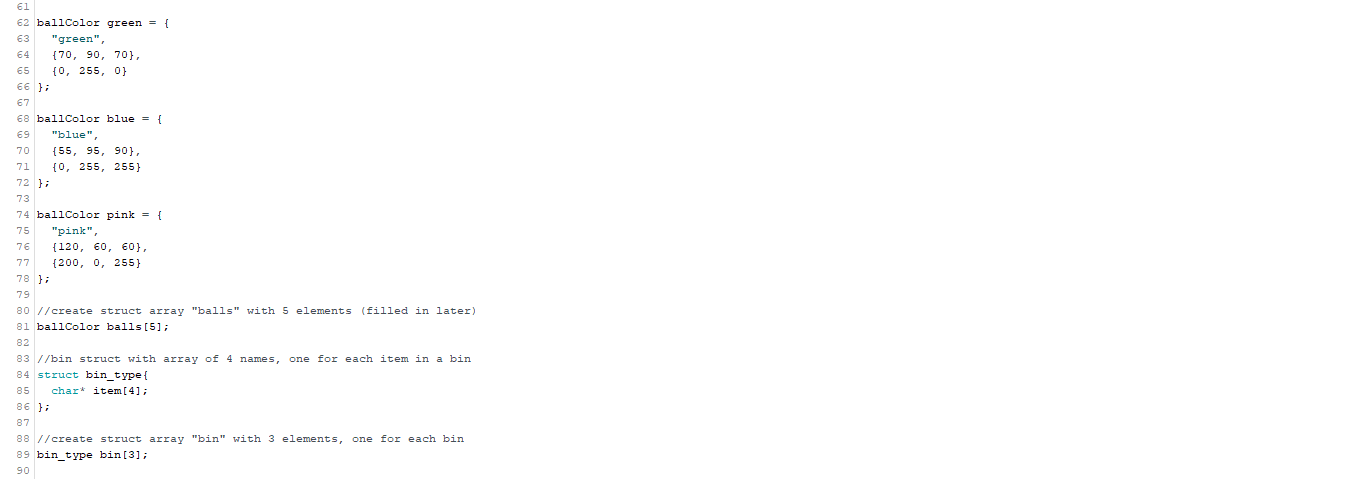
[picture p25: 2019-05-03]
LaTeX/Images/Screenshot_98.png

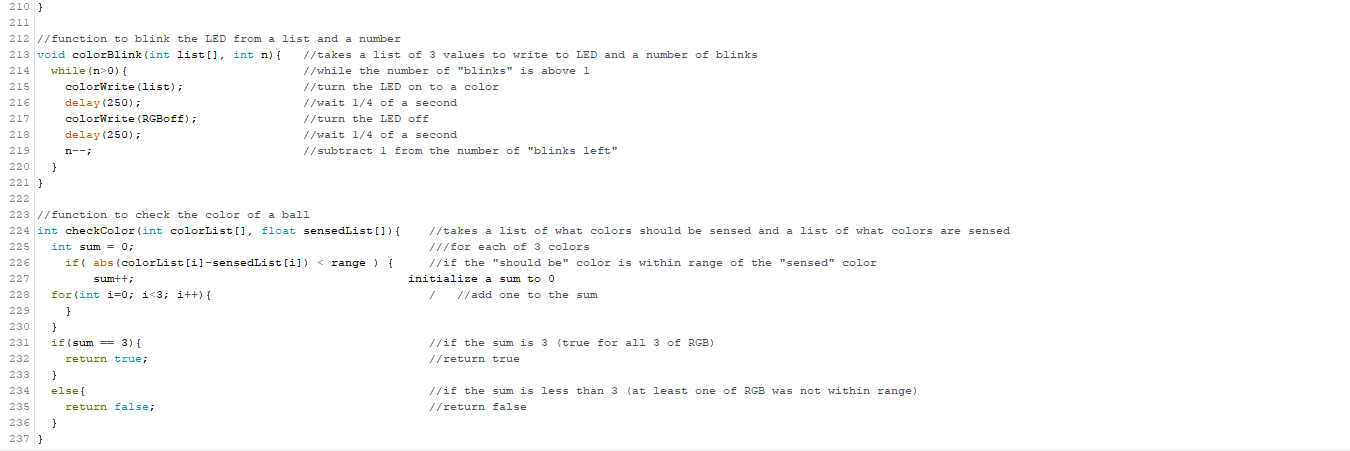
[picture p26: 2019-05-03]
LaTeX/Images/Screenshot_103.png

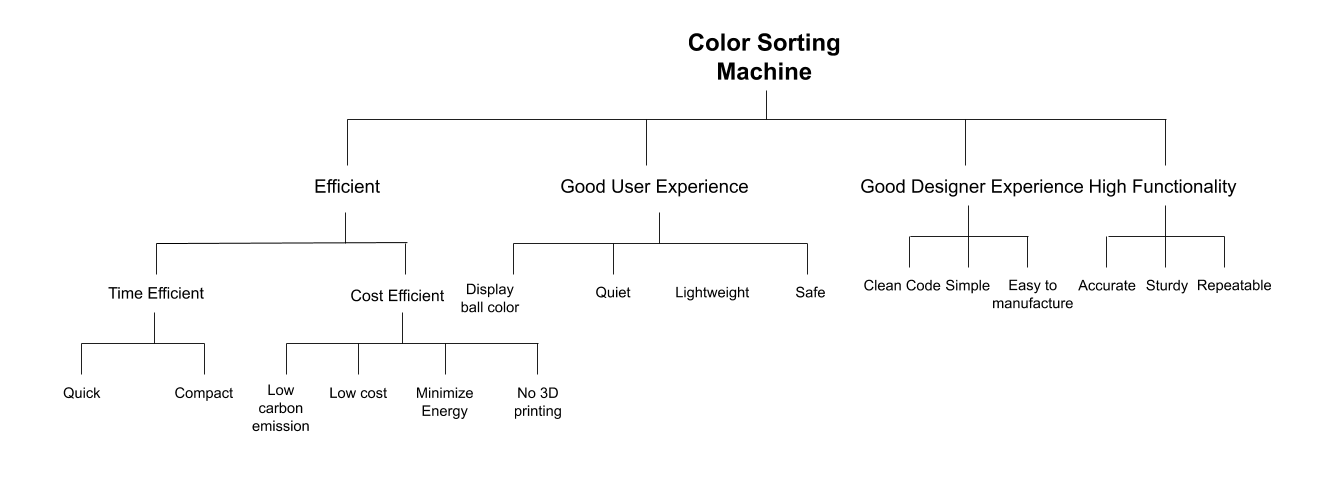
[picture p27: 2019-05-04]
LaTeX/Images/objectivestree.png

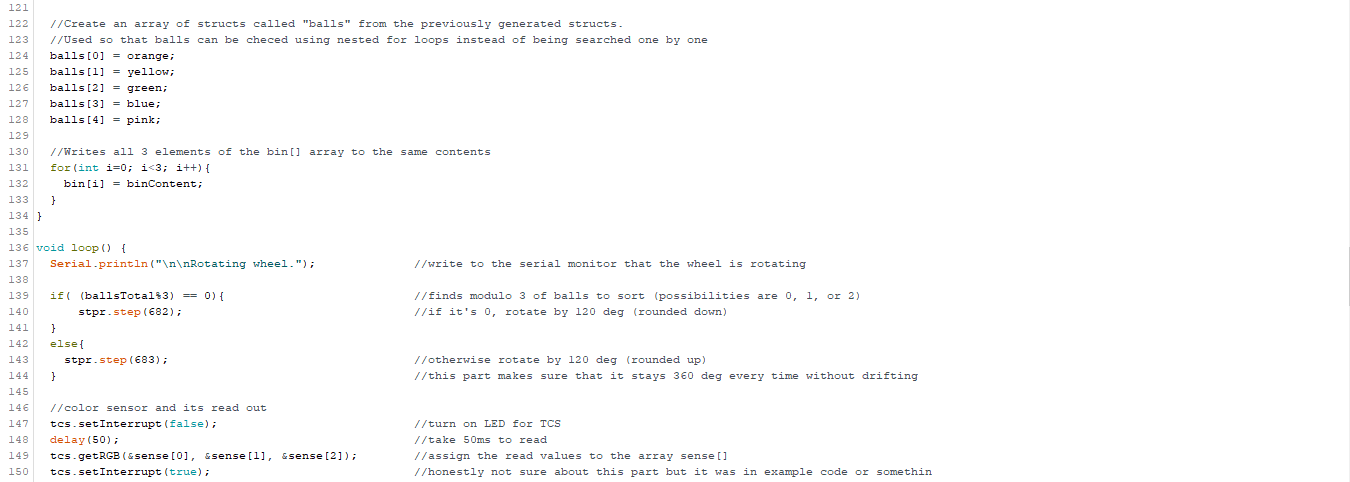
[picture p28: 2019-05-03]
LaTeX/Images/Screenshot_100.png

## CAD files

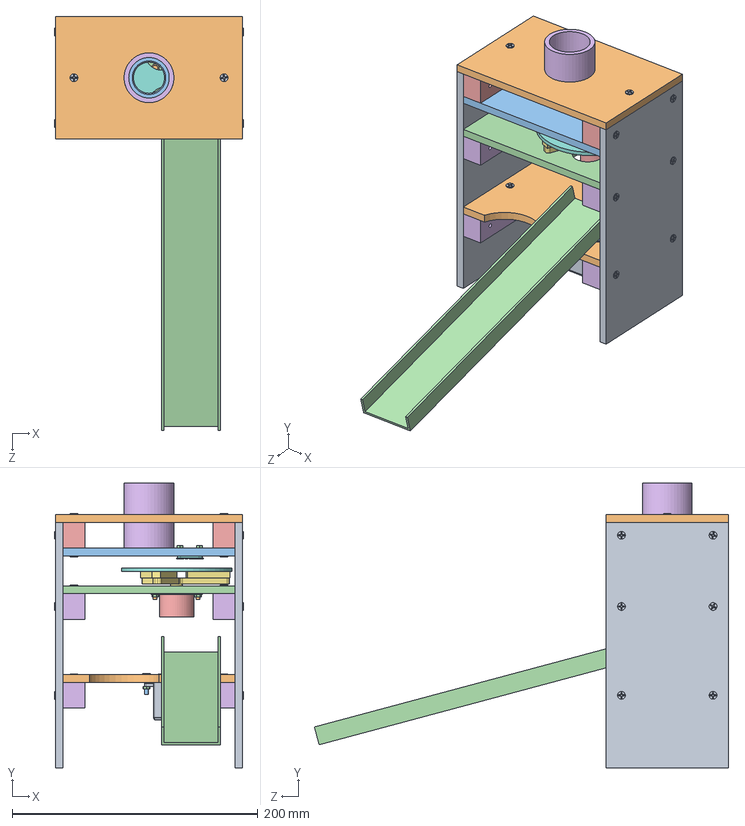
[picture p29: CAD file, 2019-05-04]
CAD/cad AS BUILT/assembly AB.SLDASM
154.3 x 232.1 x 337.4 mm
side wall AB x 2
top plate AB
upper plate AB
middle plate AB
stepper
support AB x 4
stepper horn AB
wheel AB
MG995
lower plate AB
ramp bracket AB
ramp AB
servo horn AB
coupler AB
wheel support AB x 3
tcs34725
screw AB x 20
bolt 10 x 4
bolt 16 x 4
nut x 8
support top AB x 2

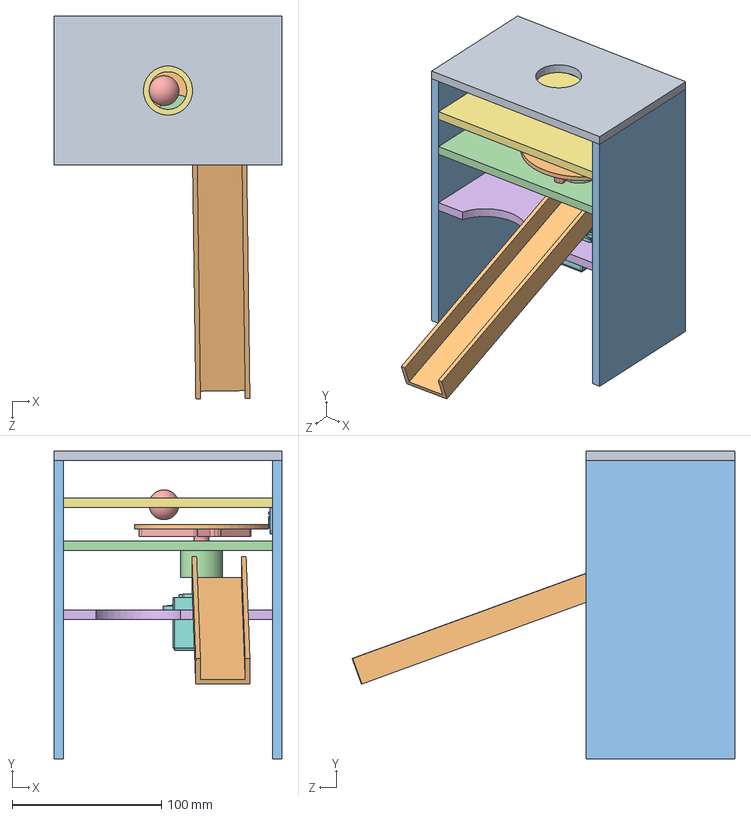
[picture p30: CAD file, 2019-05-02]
CAD/cad IN PROGRESS/assembly IP.SLDASM
152.7 x 206.4 x 256.9 mm
top plate IP
wheel IP
side wall IP x 2
middle plate IP
ball
lower plate IP
upper plate IP
MG995
ramp bracket IP
ramp IP
tcs34725
stepper
stepper horn IP

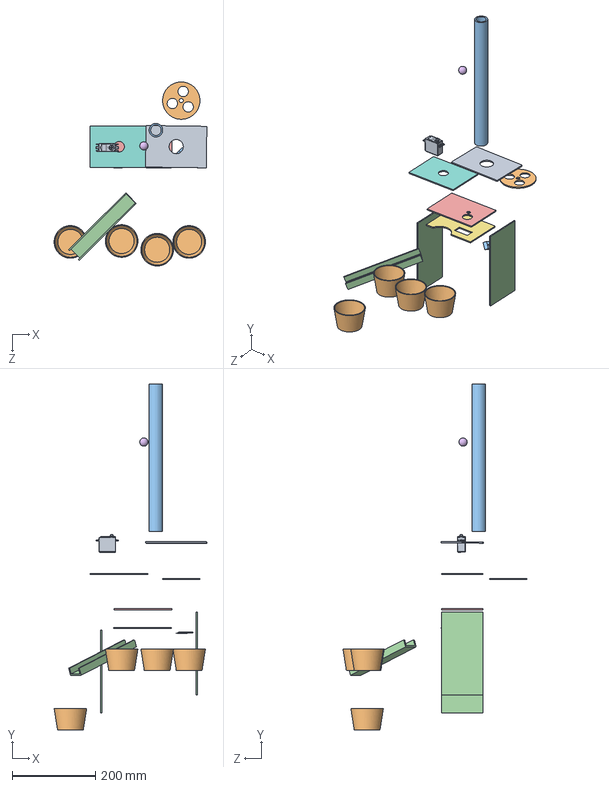
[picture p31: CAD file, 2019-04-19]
CAD/cad ORIGINAL DESIGN/disassembly.SLDASM
367.8 x 832.9 x 443.1 mm
top plate
wheel
hopper
side wall x 2
middle plate
ball
lower plate
upper plate
MG995
bin x 4
ramp bracket
ramperoni

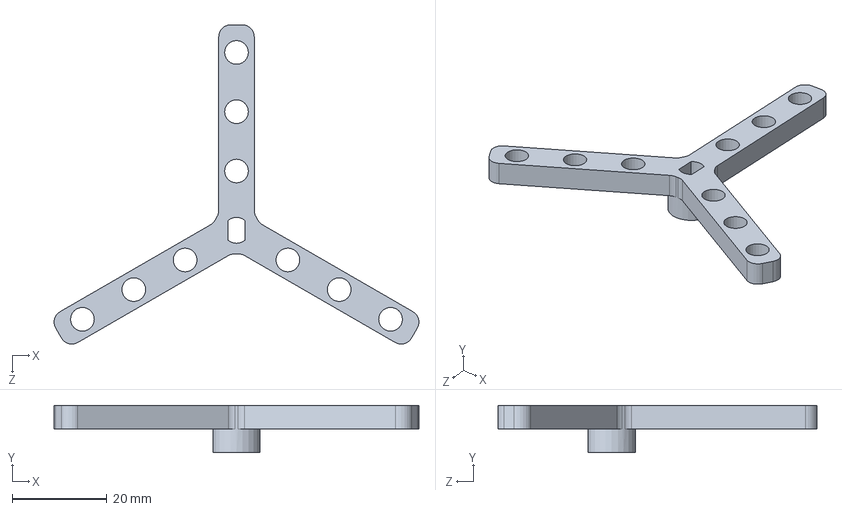
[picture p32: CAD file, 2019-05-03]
CAD/cad AS BUILT/stepper horn AB.SLDPRT
76.9 x 10.0 x 67.3 mm

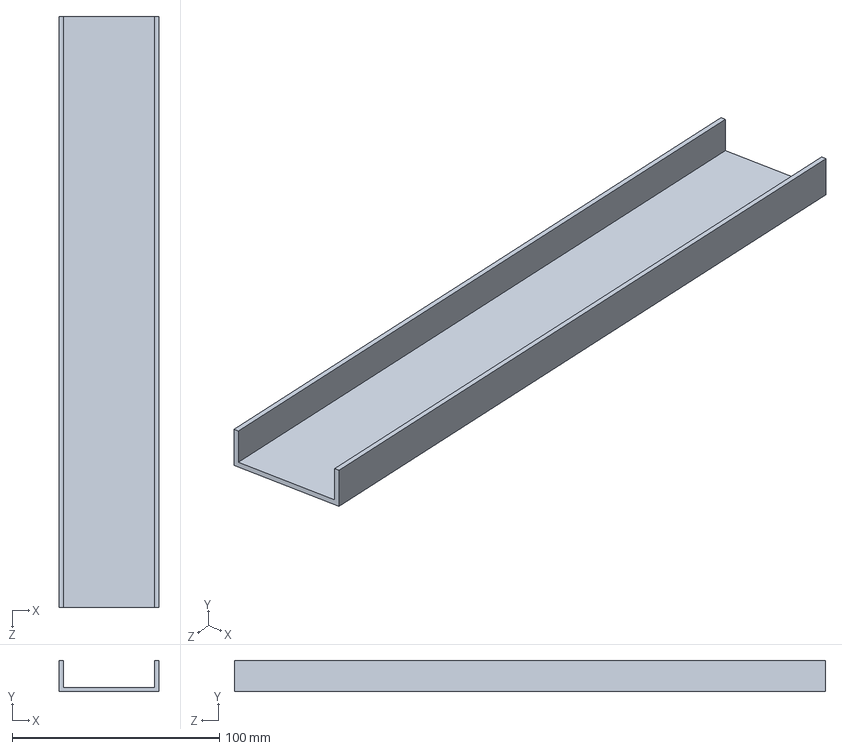
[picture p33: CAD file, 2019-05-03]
CAD/cad AS BUILT/ramp AB.SLDPRT
48.0 x 15.0 x 285.0 mm

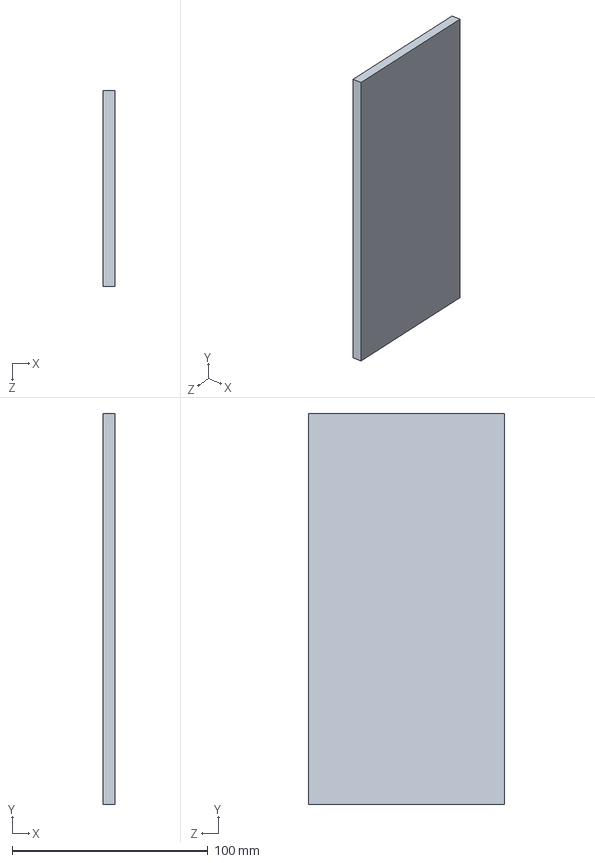
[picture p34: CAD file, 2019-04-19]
CAD/cad IN PROGRESS/side wall.SLDPRT
6.35 x 200.0 x 100.0 mm

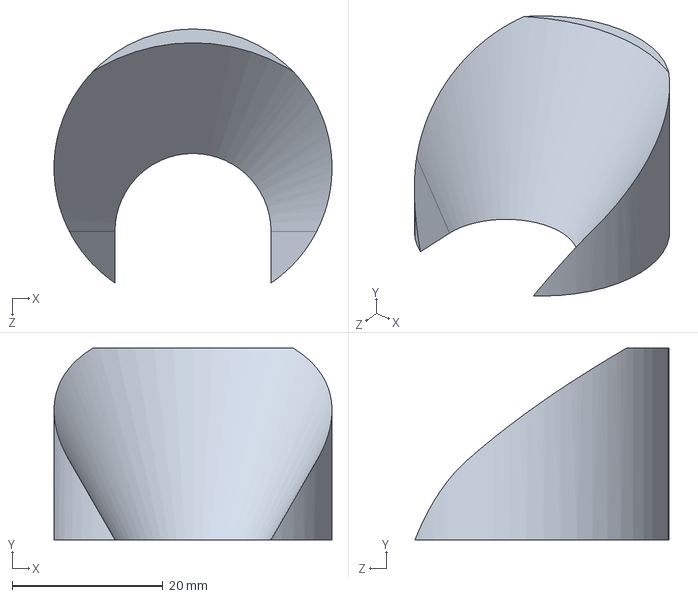
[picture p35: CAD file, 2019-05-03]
CAD/cad AS BUILT/coupler ramp AB.SLDPRT
36.8 x 25.4 x 33.7 mm

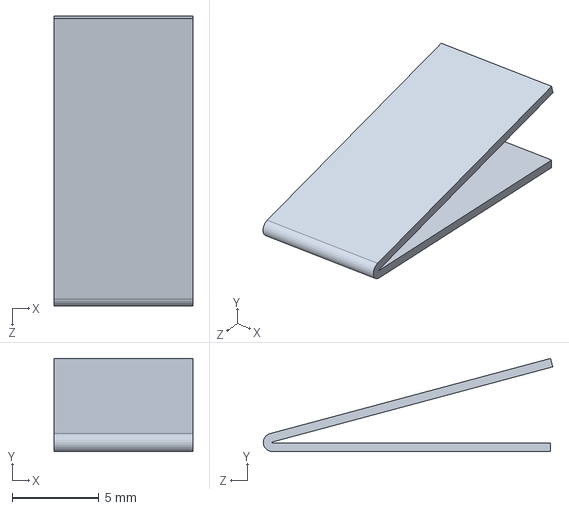
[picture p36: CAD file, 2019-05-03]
CAD/cad AS BUILT/ramp bracket AB.SLDPRT
8.00 x 5.36 x 16.7 mm

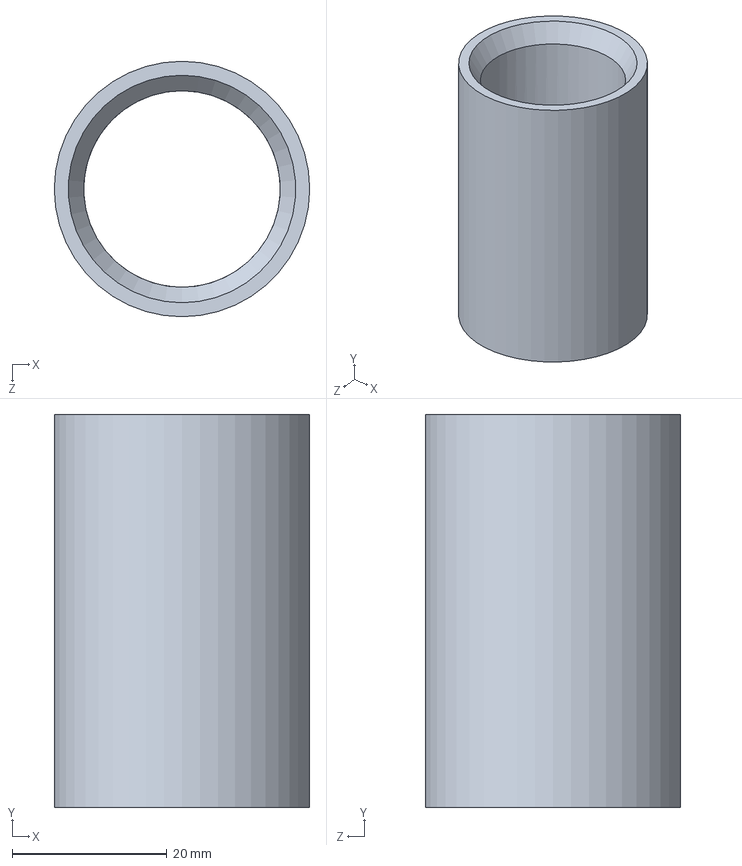
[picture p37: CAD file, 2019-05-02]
CAD/cad AS BUILT/coupler tube AB.SLDPRT
33.0 x 50.8 x 33.0 mm

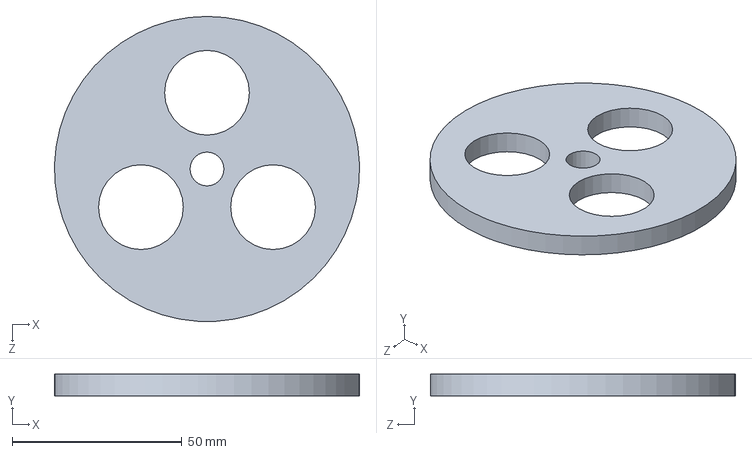
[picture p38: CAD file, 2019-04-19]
CAD/cad ORIGINAL DESIGN/wheel.SLDPRT
90.0 x 6.35 x 90.0 mm

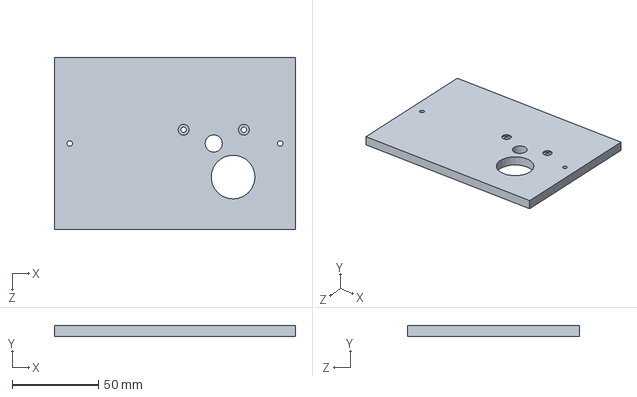
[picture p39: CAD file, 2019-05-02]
CAD/cad AS BUILT/middle plate AB.SLDPRT
140.0 x 6.35 x 100.0 mm

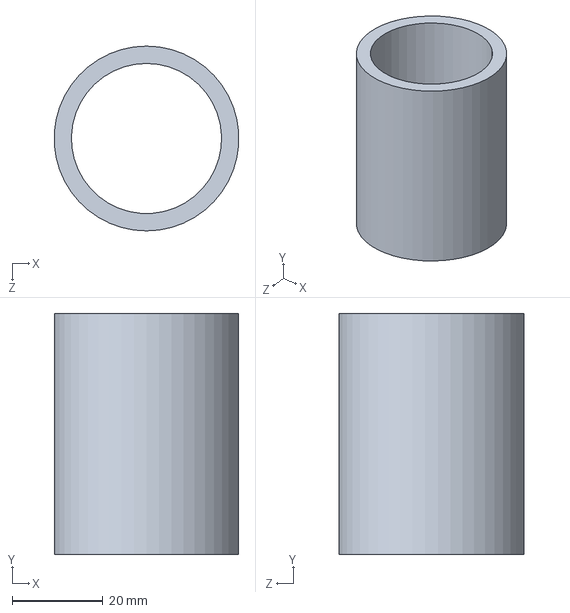
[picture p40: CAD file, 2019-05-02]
CAD/cad AS BUILT/coupler AB.SLDPRT
40.5 x 53.0 x 40.6 mm

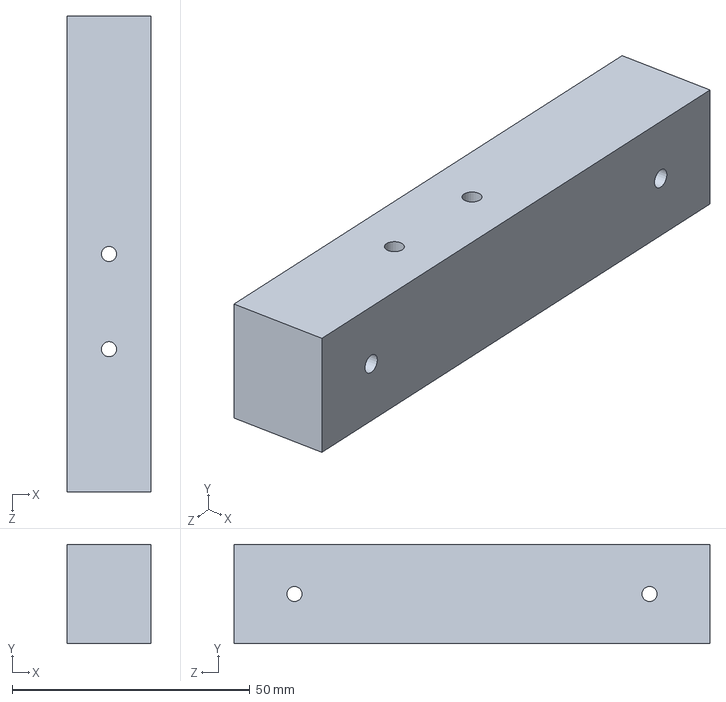
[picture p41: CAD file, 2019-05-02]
CAD/cad AS BUILT/support top AB.SLDPRT
17.7 x 20.9 x 100.0 mm

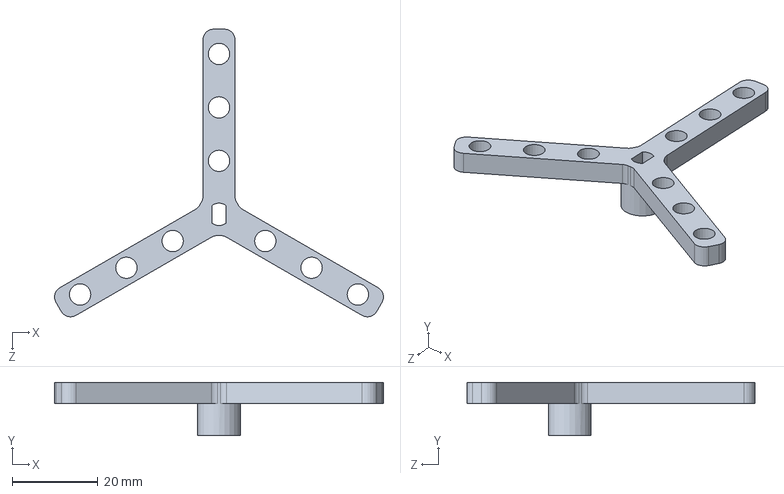
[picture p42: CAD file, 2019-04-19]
CAD/cad ORIGINAL DESIGN/stepper horn.SLDPRT
76.9 x 12.5 x 67.3 mm

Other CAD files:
CAD/cad IN PROGRESS/assembly.SLDASM
CAD/cad AS BUILT/disassembly AB.SLDASM
CAD/cad AS BUILT/coupler angle AB.SLDPRT
CAD/cad AS BUILT/upper plate AB.SLDPRT
CAD/cad AS BUILT/Group17_StepperHorn_3DPrint.STL
CAD/cad AS BUILT/Group17_Wheel_LaserCut.DXF
CAD/cad AS BUILT/MG995.SLDPRT
CAD/cad AS BUILT/ball.SLDPRT
CAD/cad AS BUILT/bin.SLDPRT
CAD/cad AS BUILT/bolt 10.SLDPRT
CAD/cad AS BUILT/bolt 16.SLDPRT
CAD/cad AS BUILT/drawings/assembly AB.SLDDRW
CAD/cad AS BUILT/drawings/mid and lower plate AB.SLDDRW
CAD/cad AS BUILT/drawings/ramp and coupler.SLDDRW
CAD/cad AS BUILT/drawings/side wall and support beams.SLDDRW
CAD/cad AS BUILT/drawings/top and upper plate AB.SLDDRW
CAD/cad AS BUILT/drawings/wheel and stepper horn.SLDDRW
CAD/cad AS BUILT/hopper.SLDPRT
CAD/cad AS BUILT/lower plate AB.SLDPRT
CAD/cad AS BUILT/nut.SLDPRT
CAD/cad AS BUILT/screw AB.SLDPRT
CAD/cad AS BUILT/servo horn AB.SLDPRT
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

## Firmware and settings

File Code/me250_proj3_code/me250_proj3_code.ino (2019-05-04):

//ME 250 Spring 2019
//Project 3: Color Sorter
// Hammad Imam/Group 17

//initialize servo + stepper motors and color sensor
#include <Servo.h>
Servo servo;
#include <Stepper.h>
#include <Adafruit_TCS34725.h>
Adafruit_TCS34725 tcs =Adafruit_TCS34725(TCS34725_INTEGRATIONTIME_50MS, TCS34725_GAIN_4X);

//CONFIG
//ALL PINS GO HERE
int red = 11;                         //
int grn = 10;                         //pins for RGBLED
int blu = 9;                          //
Stepper stpr(512, A0, A2, A1, A3);    //in the order IN1, 3, 2, 4
int servopin = 3;                     //servo pin
//TCS: SDA -> A4, SCL -> A5.          //This can't be changed (unless we really wanted to but we don't)

//initialize variables
int stepspeed = 40;                                       //speed that the stepper operates
int wheeldelay = 1500;                                    //time after the wheel rotates that the code is delayed
float sense[3];                                           //initialize an array to store the 3 values put out by the TCS
int servopos[] = {40, 60, 80, 100};                       //locations of the bins in degrees
String color = "none";                                    //initialize color to none to use as placeholder
int ballsTotal = 17;                                      //total balls to be sorted (used to make sure no balls get left in hopper/device)  
int ballsToSort = 12;                                     //this counts how many balls need to be processed, should be 0 when all balls are done
int range = 5;                                            //range from "centerpoint" defined in struct that a ball's RGB can be

//initialize colors
//make it easier for status updates using one of these 'default' colors
//less bright than other colors displayed (in theory)
int RGBwhite[] = {255, 255, 255};     //used for "done" (would pick green but it's a ball color) 
int RGBred[] = {255, 0, 0};           //used for "not done" or alerts or whatever
int RGBoff[] = {0, 0, 0,};            //used for turning the led off 

//define ball color struct with name of color, threshold for sensing, and color for LED:
//row 1: String name of color
//row 2: array {red, grn, blu} for what the ball color should show up as
//row 3: array {red, grn, blu} color to send to rgbled

struct ballColor{
  String colorName;
  int color[3];
  int RGB[3];
} ;

//assign values to structs for each ball color
ballColor yellow = {
  "yellow",
  {77, 101, 61},
  {165, 255, 0}
};

ballColor blue = {
  "blue",
  {71, 91, 81},
  {0, 255, 255}
};

ballColor pink = {
  "pink",
  {114, 74, 55},
  {200, 0, 255}
};

ballColor orange = {
  "orange",
  {127, 67, 51,},
  {255, 200, 0}
};

ballColor green = {
  "green",
  {76, 97, 70},
  {0, 255, 0}
};


//create struct array "balls" with 5 elements (filled in later)
ballColor balls[5];

//bin struct with array of 4 names, one for each item in a bin
struct bin_type{
  char* item[4];
};

//create struct array "bin" with 3 elements, one for each bin
bin_type bin[3];

//create array used to define each element of struct array "bin" (filled in later)
bin_type binContent = {
  {"pink", "pink", "yellow", "blue"}
};

void setup() {
  //initialize serial line
  Serial.begin(9600);
  
  //initialize servo motor
  servo.attach(servopin);         //attach it to previously defined servo pin
  servo.write(servopos[3]);       //write it to the trash bin to start
 
  //initialize DC motor
  stpr.setSpeed(stepspeed);       //set the speed of the stepper rotation

  //initialize pins
  pinMode (red, OUTPUT);
  pinMode (grn, OUTPUT);
  pinMode (blu, OUTPUT);
  pinMode (A4, INPUT);
  pinMode (A5, INPUT);

  //Make sure color sensor initializes
  if (tcs.begin()) {
    Serial.println("Found TCS");} 
  else {
    Serial.println("No TCS34725 found ... check your connections");
    while(1); // halt!
  }
  
  //Create an array of structs called "balls" from the previously generated structs.
  //Used so that balls can be checed using nested for loops instead of being searched one by one
  balls[0] = yellow;
  balls[1] = blue;
  balls[2] = pink;
  balls[3] = orange;
  balls[4] = green;

  //Writes all 3 elements of the bin[] array to the same contents
  for(int i=0; i<3; i++){
    bin[i] = binContent;
  }
}

void loop() {
  Serial.println("\n\nRotating wheel.");              //write to the serial monitor that the wheel is rotating
  
  if( (ballsTotal%3) == 0){                           //finds modulo 3 of balls to sort (possibilities are 0, 1, or 2)
      stpr.step(682);                                 //if it's 0, rotate by 120 deg (rounded down)
  }                                                   
  else{
    stpr.step(683);                                   //otherwise rotate by 120 deg (rounded up)
  }                                                   //this part makes sure that it stays 360 deg every time without drifting
  
  //color sensor and its read out
  tcs.setInterrupt(false);                            //turn on LED for TCS
  delay(50);                                          //take 50ms to read
  tcs.getRGB(&sense[0], &sense[1], &sense[2]);        //assign the read values to the array sense[]
  tcs.setInterrupt(true);                             //honestly not sure about this part but it was in example code or somethin           

  //Checking the color of the ball
  colorBlink(RGBred, 3);                              //blink the led to show that the scan is starting
  for(int i=0; i<5; i++){                             //for every color possible
    Serial.println(balls[i].colorName);               //display the color being checked to the serial monitor
    if( (checkColor(balls[i].color, sense)) ){        //if the sensed color matches a ball (see below for details on checkColor function)
        Serial.println("Ball found!");                //display that a ball was found
        color = balls[i].colorName;                   //set the color string to the name of the color
        colorBlink(RGBwhite, 1);                      //blink the led white once
        colorBlink(balls[i].RGB, 3);                  //blink the led with the sensed color
        ballsTotal--;                                 //subtract one from the total number of balls
        break;                                        //exit the for loop 
    }
   else{                                              //otherwise,
      color = "none";                                 //set the color string to "none"
      colorBlink(RGBred, 1);                          //blink the led red once to show that it's working
    }
  }

  //Printing what was detected to serial monitor
  Serial.println("\nR: " + String(sense[0]) + "\t G: " + String(sense[1]) + "\t B:" + String(sense[2]));  //print the RGB values to the serial monitor
  Serial.println("Ball detected: " + String(color) + "\n");                                               //print the sensed ball to the serial monitor

  //Routing the ball to the correct bin/trash
  [&]{
    for(int i = 0; i<3; i++){                                                                           //for each bin (3 total)
      for(int j = 0; j<4; j++){                                                                         //for each spot in the bin (4 total)
        Serial.println("Bin " + String((i+1)) + ", Item " + String(j+1) + " is " + bin[i].item[j]);     //write what is in that spot (total of 12 spots)
        if(String(bin[i].item[j]) == String(color)){                                                    //if the sensed ball matches one of the colors
          servo.write(servopos[i]);                                                                     //move the servo to the bin
          Serial.println("Servo set to bin " + String(i+1));                                            //display what bin the servo is set to
          bin[i].item[j] = "done";                                                                      //"cross off" the spot by changing the array value to "done"
          ballsToSort--;                                                                                //subtract one from the number of balls sorted
          Serial.println("Bin " + String(i+1) + ", item " + String(j+1) + " done.");                    //display the spot in the bin is complete
          Serial.println("Balls Left to Sort: " + String(ballsToSort));                                 //display # of balls left to sort
          colorBlink(RGBwhite, 3);                                                                      //flash that a ball has been sorted correctly
          return;                                                                                       //exit both for loops by exiting the [&] flag
        }                                       
      }                                         //"else" if the sensed ball does not match any of the required balls
    }                                           //(if the conditional is never true it doesn't leave the [&] flag before this part runs)                      
    servo.write(servopos[3]);                   //move the servo to the trash bin
    Serial.println("Servo set to trash");       //display that the servo has been moved to the trash
    return;                                     //exit
  }();

  Serial.println("Balls left in hopper: " + String(ballsTotal));  //display how many balls are left in the hopper

  if( (ballsToSort==0) && (ballsTotal == 0)){         //if all balls have been sorted and there are no balls left in the hopper
    Serial.println("\n\nDone.");                      //print that the sorting is done
    colorWrite(RGBwhite);                             //turn the LED white
    while(1);                                         //stop running
  }
}

//FUNCTIONS USED IN CODE ABOVE 

//function to write the color from a list to a RGBLED
void colorWrite(int list[]){    //takes a list of 3 values to write to LED
  analogWrite(red, list[0]);
  analogWrite(grn, list[1]);    //takes each list element and writes it to an led
  analogWrite(blu, list[2]);
}

//function to blink the LED from a list and a number
void colorBlink(int list[], int n){   //takes a list of 3 values to write to LED and a number of blinks 
  while(n>0){                         //while the number of "blinks" is above 1
    colorWrite(list);                 //turn the LED on to a color
    delay(250);                       //wait 1/4 of a second
    colorWrite(RGBoff);               //turn the LED off
    delay(250);                       //wait 1/4 of a second
    n--;                              //subtract 1 from the number of "blinks left"
  }
}

//function to check the color of a ball
int checkColor(int colorList[], float sensedList[]){        //takes a list of what colors should be sensed and a list of what colors are sensed
  int sum = 0;                                              //initialize a sum to 0   
  for(int i=0; i<3; i++){                                   //for each of 3 colors
        if( abs(colorList[i]-sensedList[i]) < range ) {     //if the "should be" color is within range of the "sensed" color
        sum++;                                              //add one to the sum
    }
  }
  if(sum == 3){                                         //if the sum is 3 (true for all 3 of RGB)
    return true;                                        //return true
  }
  else{                                                 //if the sum is less than 3 (at least one of RGB was not within range)
    return false;                                       //return false
  }
}

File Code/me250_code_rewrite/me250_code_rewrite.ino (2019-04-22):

//initialize servo + stepper motors and color sensor
#include <Servo.h>
Servo servo;
#include <Stepper.h>
#include <Adafruit_TCS34725.h>
Adafruit_TCS34725 tcs =Adafruit_TCS34725(TCS34725_INTEGRATIONTIME_50MS, TCS34725_GAIN_4X);

//CONFIG

//ALL PINS GO HERE
int red = 11;
int grn = 10;
int blu = 9;
Stepper stpr(512, A0, A1, A2, A3);
int servopin = 3;
//TCS: SDA -> A4, SCL -> A5.  This can't be changed (unless we really wanted to but we don't)


//initialize variables
int stepspeed = 40;                                       //speed that the stepper operates
float sense[3];                                           //initialize the 3 values put out by the TCS
int blinknum = 5;                                         //how many times the LED will blink when signalling (unless custom number used)
int servopos[] = {35, 70, 105, 140};                      //locations of the bins
char color = "none";                                      //initialize color to none to use as placeholder
int ballsLeft = 12;                                       //this counts how many balls need to be processed, should be 0 when all balls are done

//initialize colors
//make it easier for status updates using one of these 'default' colors
//less bright than other colors displayed (in theory)
int RGBwhite[] = {128, 128, 128};     //used for "done" (would pick green but it's a ball color) 
int RGBred[] = {128, 0, 0};           //used for "not done" or alerts or whatever
int RGBoff[] = {0, 0, 0,};            //used for turning the led off 


//color thresholds + values to display as structs:
//row 1: String name of color
//row 2: array {red low, red high, grn low, grn hi, blu low, blu hi} for color read thresh
//row 3: array {red, grn, blue} color to send to rgbled

struct ballColor{
  char color;
  int thresh[6];
  int RGB[3];
} ;

ballColor orange = {
  "orange",
  {139, 149, 52, 62, 36, 46},
  {0, 255, 255}
};

ballColor yellow = {
  "yellow",
  {58,68,106,116,55,65},
  {0, 255, 255}
};

ballColor green = {
  "green",
  {48, 58, 111, 121, 63, 73},
  {0, 255, 0}
};

ballColor blue = {
  "blue",
  {41, 51, 90, 100, 95, 105},
  {0, 255, 255}
};

ballColor pink = {
  "pink",
  {150, 160, 42, 52, 41, 71},
  {170, 0, 255}
};

ballColor balls[5];

//setup bins as an array of 3 structs
struct bin_type{
  char* item[3];
};

bin_type bin[3];

bin_type binContent = {
  {"pink", "pink", "yellow", "blue"}
};

//!!!!!!!!!!!!!!!!!!!!!!!!!!!!!!!!!!!!!!!!!!!!!!!!!!!!!!!!!!!!
//!!!!!!!!!!!!!!!!!!!!!!!!!!!!!!!!!!!!!!!!!!!!!!!!!!!!!!!!!!!!
//!!!!!IF TESTING DO NOT CHANGE ANYTHING BELOW THIS POINT!!!!!
//!!!!!!!!!!!!!!!!!!!!!!!!!!!!!!!!!!!!!!!!!!!!!!!!!!!!!!!!!!!!
//!!!!!!!!!!!!!!!!!!!!!!!!!!!!!!!!!!!!!!!!!!!!!!!!!!!!!!!!!!!!


void setup() {
  //initialize serial line
  Serial.begin(9600);
  
  //initialize servo motor
  servo.attach(servopin);
  servo.write(0);
 
  //initialize DC motor
  stpr.setSpeed(stepspeed);

  //initialize pinouts
  pinMode (red, OUTPUT);
  pinMode (blu, OUTPUT);
  pinMode (grn, OUTPUT);
  pinMode (A4, INPUT);
  pinMode (A5, INPUT);

  //for color sensor
  if (tcs.begin()) {
    Serial.println("Found sensor");} 
  else {
    Serial.println("No TCS34725 found ... check your connections");
    while (1); // halt!
  }


  //Create an array of structs called "balls" from the previously generated structs.
  //I'm aware this is a bit redundant, but it helps keep the user defined variables
  //all in one place up above, as well as more concise since the whole struct can be
  //defined at once instead of needing to be done as each individual value.
  balls[0] = orange;
  balls[1] = yellow;
  balls[2] = green;
  balls[3] = blue;
  balls[4] = pink;

  //Similar to above but with the bins
  //Use for 3 identical bins with the same content
  for(int i=0; i<3; i++){
    bin[i] = binContent;
  }
}

void loop() {
  stpr.step(683);           //stepper motor rotates 120deg (IF WE DO 3 HOLES, WE WILL HAVE 0.3 DEGREE OFF FOR EACH BALL
  delay(1500);              //waits 1.5 seconds just to give shit time to work
  
  //color sensor and its read out
  tcs.setInterrupt(false);                        //turn on LED
  delay(50);                                      //takes 50ms to read
  tcs.getRGB(&sense[0], &sense[1], &sense[2]);    //assign the read values to the array sense[]
  tcs.setInterrupt(true);                         //

  colorBlink(RGBred, 3);`

  //check color of the ball
  for(int i = 0; i<5; i++){                       //for every color possible
    if(checkColor(balls[i].thresh, sense) ){      //if the sensed color is within the threshold
        color = balls[i].color;                   //set the color string to the name of the color
        colorBlink(balls[i].RGB, blinknum);       //blink the led with the sensed color
        break;                                    //exit the for loop if one is found
    }
    else{
      color = "none";
    }
  }

  //print to serial monitor
  Serial.println("R: " + String(sense[0]) + "\t G: " + String(sense[1]) + "\t B:" + String(sense[2])); //print the RGB values to the serial monitor
  Serial.println(color);                          //print the sensed color to the serial monitor

  //routing the ball
  for(int i = 0; i<3; i++){                   //for each bin (3 total)
    for(int j = 0; i<3; i++){                   //for each color desired in the bin (3 total)
      if(bin[i].item[j] == color){                //if the sensed ball matches one of the colors
        servo.write(servopos[i]);                   //move the servo to the bin
        bin[i].item[j] = "";                        //"cross off" the ball that was guided by changing the array value to null
        ballsLeft--;                                //reduce number of balls left by 1
        break;
        break;                                      //exit both for loops 
      }
      else{                                       //else (if the sensed ball does NOT match a color in the list)
        servo.write(servopos[3]);                   //move the servo to the trash bin
      }
    }
  }
}

//function to write the color to a 
void colorWrite(int list[]){
  analogWrite(red, list[0]);
  analogWrite(grn, list[1]);
  analogWrite(blu, list[2]);
}

void colorBlink(int list[], int n){
  while(n>0){
    colorWrite(list);
    delay(250);
    colorWrite(RGBoff);
    delay(250);
    n--;
  }
}

int checkColor(int colorList[], float sensedList[]){
  int sum = 0;
    for(int i=0; i<3; i++){
      if(colorList[(2*i)] <= sensedList[i] && sensedList[i] <= colorList[(2*i + 1)]){
        sum++;
    }
  }
  if(sum = 3){
    return true;
  }
  else{
    return false; 
  }
}

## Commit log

2019-04-19 initial commit with files
    [MG995.SLDPRT, assembly drawing.SLDDRW, assembly.SLDASM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]
2019-04-19 added different versions of CAD drawings
    [Group17_StepperHorn_3DPrint.STL, Group17_Wheel_LaserCut.DXF, MG995.SLDPRT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]
2019-04-19 changed part of code, added servo test
2019-04-22 added more stop conditions, changed some values
    [hopper.SLDPRT]
2019-04-22 changed servo's neutral value
2019-04-22 differentiated between OLD and IP cad files
    [assembly - device only.SLDASM, assembly IP (2).SLDDRW, assembly IP.SLDASM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]
2019-04-24 fixed binContent value
    [Group17_StepperHorn_3DPrint.STL, Group17_Wheel_LaserCut.DXF, MG995.SLDPRT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]
2019-04-24 worked on AB assembly, fixed some code errors
    [assembly AB.SLDASM]
2019-04-24 fixed color reading, fixed bin checking
    [me250_proj3_code.ino]
2019-04-24 working prototype of code that scans and sorts properly
2019-04-29 minor changes to CAD and code
    [assembly AB.SLDASM, lower plate AB.SLDPRT, middle plate AB.SLDPRT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]
2019-05-01 Changed test files, fixed stepper drift
    [me250_proj3_code.ino, test_rgbled.ino, test_servostepper.ino]
2019-05-01 changed ramp sections
    [assembly AB.SLDASM, ramp AB.SLDPRT, ramp bracket AB.SLDPRT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]
2019-05-01 changed how stepper drift was handled
    [me250_proj3_code.ino]
2019-05-01 fixed ramp bracket to better reflect actual
    [assembly AB.SLDASM, ramp bracket AB.SLDPRT]
2019-05-01 updated wheel assembly, updated coupler
    [assembly AB.SLDASM, coupler AB.SLDPRT, coupler ramp AB.SLDPRT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]
2019-05-01 added screws to assembly
    [assembly AB.SLDASM, screw AB.SLDPRT, tcs34725.sldprt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]
2019-05-02 worked on CAD drawings
    [assembly AB.SLDASM, assembly AB.SLDDRW, assembly IP.SLDASM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]
2019-05-02 testing + CAD
    [mid and lower plate AB.SLDDRW]
2019-05-03 Fixed comments in code
    [me250_proj3_code.ino]
2019-05-03 Added images
    [Group17_StepperHorn_3DPrint.STL, Group17_Wheel_LaserCut.DXF, MG995.SLDPRT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]
2019-05-03 updated CAD
    [Group17_StepperHorn_3DPrint.STL, Group17_Wheel_LaserCut.DXF, MG995.SLDPRT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]
2019-05-03 final testing and drawings
    [assembly AB.SLDASM, assembly AB.SLDDRW, coupler ramp AB.SLDPRT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]
2019-05-03 worked on drawings
    [assembly AB (2).SLDDRW, assembly AB.SLDASM, assembly AB.SLDDRW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]
2019-05-04 added BOM drawings
    [assembly AB.SLDASM, assembly AB.SLDDRW]
